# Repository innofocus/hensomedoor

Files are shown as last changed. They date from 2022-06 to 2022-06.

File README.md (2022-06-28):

# hensomedoor
An handsome door for any hen house.
## Object
This is an automated servo mecanism based on internal weight sensor. The prototype served as an chicken house door.

## Principle
The main concept here is the servo's frame as a scale load strain gauge cell based :
hensomedoor v3 1_load_cell

## Description
A load is attached with a string on the axel of the servo to be driven up and down.
The servo is mounted on a load cell with strain-gauge sensor based frame.  
When apparent weight changes, the program reacts consequently.  

The code as the ability to sense the apparente weight of the servo's load (a wood door for instance) and decide what would be done :
- When the weight increases, the load arrives at maximum position, then stop the servo and set maximum position reached.
- When the weight decreases, the load arrives at minimum position, then stop the servo and set minimum position reached.
proto

## Features
The demonstration code is able to do :
- Connect to Wifi
- Web configuration with web interface
- Save the configuration to eeprom
- MQTT: send weight measured at the load cell to an mqtt server with influxdb and grafana for consultation or survey.
- Auto Setup: the current time and date setup at start from a public google script (seen gs/today) - publish at https://script.google.com/macros/s/AKfycby4gVz61EkTZBC5z9TyoYlJeNqo9d11Pdx8pyHc9pY9mqzpYZr4/exec
- Future ability to use google calendar for long scheduling, or sun dawn/rise synchronisation
- OTA update : in order to update the firmware without any cable

## web interface
The main page allows to:
- open or close the door
- read the weight
- read the current status open/close
- set opening and closing time schedule
pageroot

The config page let:
- fine tune parameters
- open or close by increment
- tare the load weight
- play with detector's parameters
config

## Building one
List of materials:
- ESP8266
- SG10 servo motor
- voltage regulators for ESP and servo
- HX711 module
- 4 strain gauge resistors
- cyanoacrylate to glue strain gauge resistors on load cell 3D printed frame.
- tiny wires for strain gauge soldering (ones from wired ear plug are perfect).
See 3D STL files to print the complete box.  

This is my chicken house's door at work :  
opening
closing

## Todos and ongoings
- add electronic schema
- write clean object code

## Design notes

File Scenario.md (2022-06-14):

samplepers = 10
samplenb = 5
sampledur = samplepers / samplenb
stddevmax = 10
speed_slow = 3
speed_fast = 8
w_zero = 10
w_precision = 30
w_delta = 100

# Initialisation
drectioned = 0
tared = 0

## Tare
### setup : door not wooked, no weight
tare = tare
tared = 1

## direction
## setup : door not hooked
## small weight arround 20g (< w_delta) or pinched with fingers
motor_up
while weight not increasing:
directioned = 1

## door weight
motor down 
wait 3
motor stop
w_door = mean(4s)
w_stdd = stdd(4s)

# door weight down
# door time to close
t0
motor down 
while weight == w_door +- w_precision
    mean update
    stdd_update
w_door_down = mean
w_door_down_stdd = stdd
while weight > w_zero
motor stop
t_door_closing = now - t0

# door weight up
# door time to open
t0
motor up
wait 3
while weight == w_door +- w_precision
   mean update
   stdd update
w_door_up = mean
w_door_up_stdd = stdd
while weight < w_door + w_precision + w_delta
    wait
motor stop
t_door_opening = now - t0

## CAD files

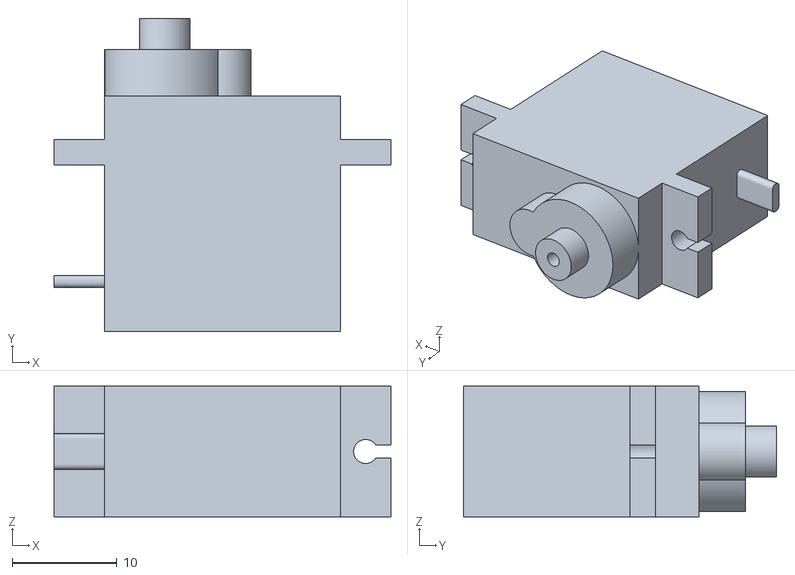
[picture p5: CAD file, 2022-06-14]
stl/hensomedoor v3.1_motor mock.stl
32.3 x 30.0 x 12.5

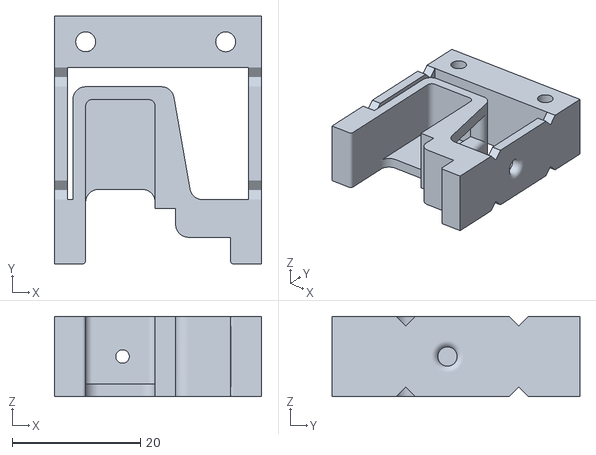
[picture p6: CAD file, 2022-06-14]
stl/hensomedoor v3.1_load_cell.stl
32.3 x 38.6 x 12.5

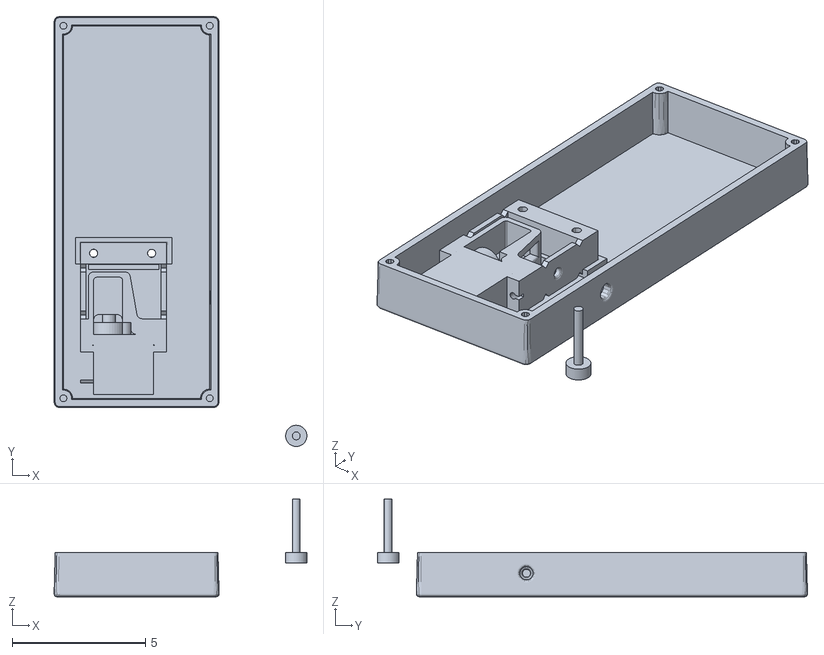
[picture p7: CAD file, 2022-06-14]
stl/hensomedoor v3.1.stl
9.50 x 16.2 x 3.67

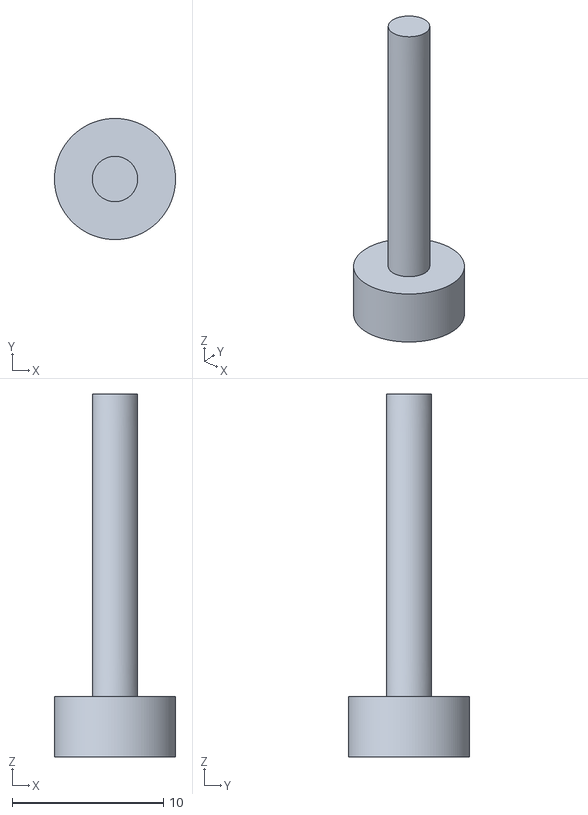
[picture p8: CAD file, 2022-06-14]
stl/hensomedoor v3.1_Part1.stl
8.00 x 8.01 x 24.0

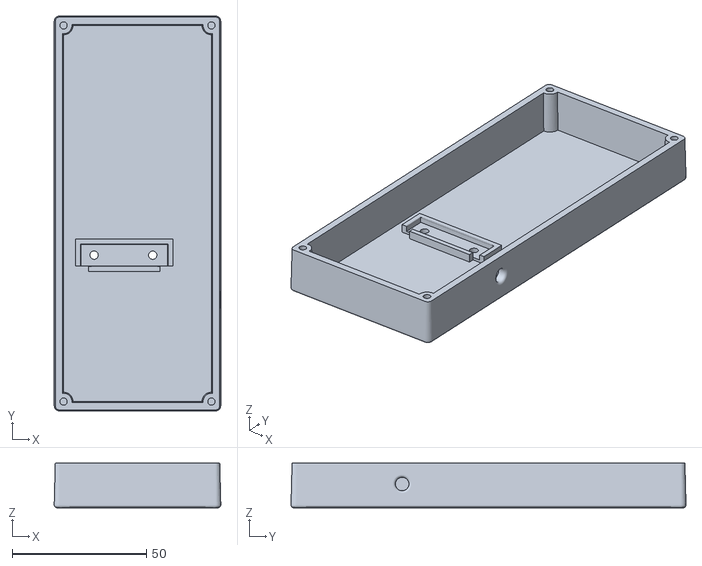
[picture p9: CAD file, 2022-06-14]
stl/hensomedoor v3.1_box_down.stl
62.0 x 147.0 x 16.6

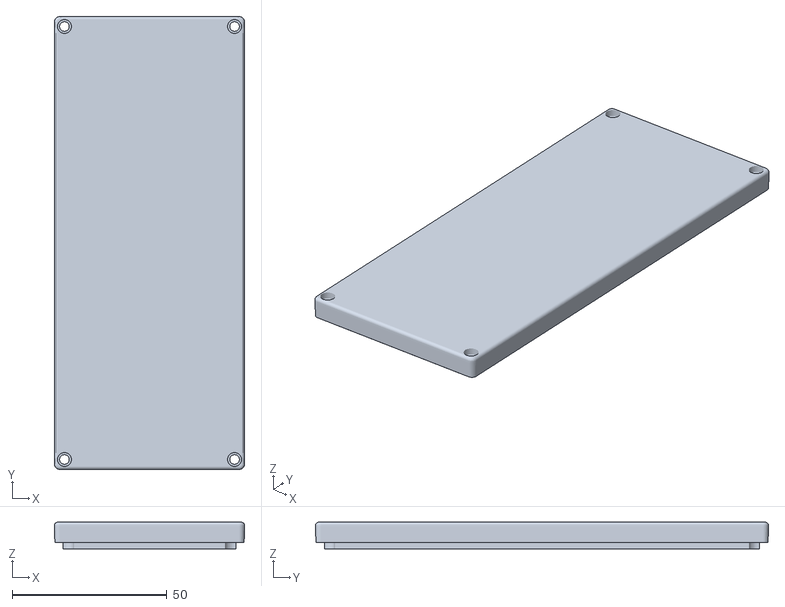
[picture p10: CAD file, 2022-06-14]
stl/hensomedoor v3.1_top_box.stl
61.5 x 146.5 x 8.60

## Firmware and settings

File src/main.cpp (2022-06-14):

#include <Arduino.h>
//networking
#include <ESP8266WiFi.h>
#include <WiFiClient.h>
#include <ESP8266WebServer.h>
#include <ESP8266mDNS.h>
#include <ESP8266HTTPUpdateServer.h>
#include <ArduinoOTA.h>

//ntp
#include <NTPClient.h>
#include <WiFiUdp.h>

//googlescript
#include <HTTPSRedirect/HTTPSRedirect.h>
#include <HTTPSRedirect/DebugMacros.h>

//servo
#include <Servo.h>

//json
#include <ArduinoJson.h>

//timer0 ticker
#include <Ticker.h>

//scale
#include <HX711.h>

//mqtt
#include <PubSubClient.h>

// configuration
#include <EEPROM.h>
#define CONFIG_SIZE 1024
#define CONFCHK 123425321

struct config_st {
  int  confchk;

  char host[32];
  char ssid[32];
  char psk[64];

  char mqttserver[32];
  int  mqttport;
  char mqtttopic[16];

  float scale;
  float scale_offset;
  int  w_closed;
  int  w_precision;
  int  w_delta;
  float  w_stdd_threshold;
  float w_door;
  int w_delta_open;
  int w_delta_close;

  int dooropened;
  int doorclosed;
  int door_h_close;
  int door_m_close;
  int door_h_open;
  int door_m_open;

  int servo_neutral;
  int servo_rotation;
  int speed_slow;
  int speed_fast;

  int configured;
};

config_st config;

// default values
#ifndef HOST

  #define HOST "hensomedoor"
  #define SSID "myssid"
  #define PSK  "myssidpassword"

  #define NTPSERVER "fr.pool.ntp.org"

  #define MQTTSERVER "mymqttserver.somewhere.net"
  #define MQTTPORT 1883
  #define MQTTTOPIC "hensomedoor"

  #define W_ZERO 10
  #define W_PRECISION 10
  #define W_DELTA 100
  #define W_DELTA_OPEN 75
  #define W_DELTA_CLOSE 100
  #define SCALE 3800.0f
  #define SCALE_OFFSET 0.0f
  #define W_DOOR 400
  #define W_STDD_THRESHOLD 1000.0f

  #define DOOR_OPENED false
  #define DOOR_CLOSED false
  #define DOOR_H_CLOSE 19
  #define DOOR_M_CLOSE 00
  #define DOOR_H_OPEN 8
  #define DOOR_M_OPEN 0

  #define SERVO_STOP 92
  #define SERVO_ROTATION -1
  #define SPEED_SLOW 4
  #define SPEED_FAST 10

  #define CONFIGURED 0

  #define SCALE_PERIOD 100
  #define SCALE_MEASURES 10

#endif



//web server
ESP8266WebServer server(80);
ESP8266HTTPUpdateServer httpUpdater;

//ntp
WiFiUDP ntpUDP;

//ntp
NTPClient timeClient(ntpUDP, NTPSERVER, 7200, 60000);

//led
#define LED 4

//motor params
#define SERVO_PIN 2
Servo servo;
Ticker ticker;

//interrupts
#define INTERRUPTPIN 00
volatile byte interrup = false;
int nbinterrupt = 0;

//load cell
// HX711 circuit wiring
#define LOADCELL_DOUT_PIN 13
#define LOADCELL_SCK_PIN 12
#define LOADCELL_SCALE 64
HX711 scale;
float scalevalue;
float scalemean;
float scalestdd;
float scalevalues[SCALE_MEASURES];
int   scaleincreases = false;
int   scaledecreases = false;
int   scaleevolution = 0;
byte scaleindex = 0;


//mqtt
WiFiClient netclient;
PubSubClient mqttclient(netclient);

//RTC
// json from google doc
String json;
int hour_ref;
int min_ref;
int sec_ref;
int hour_now = 0;
int min_now = 0;

//command control
int action_running = false;

//code

void slog(const char msg[]) {
  Serial.println(msg);
}

void save_config() {
  EEPROM.put(0, config);
  if (EEPROM.commit())  {
    slog("save_config done");
  }
  else {
    slog("save_config error");
  }
}


void ConfigPage(const char message[]) {
  digitalWrite(LED, 1);
  const int sizebuf = 2000;
  char temp[sizebuf];
  int sec = millis() / 1000;
  int min = sec / 60;
  int hr = min / 60;

  const char* pageroot = "<html>\
  <head>\
    <meta name=\"viewport\" content=\"width=device-width\" />\
    <title>HSD</title>\
    <style>\
      body { background-color: #cccccc; font-family: Arial, Helvetica, Sans-Serif; Color: #000088; }\
    </style>\
  </head>\
  <body>\
     <h1>Hen Some Door!</h1>\
    <p>Uptime: %02d:%02d:%02d</p>\
    %s\
    <form name=\"config\" method=\"post\" action=\"/config\">\
    <table><tbody>\
      <tr><td>w_stdd_threshold </td><td><input type=\"text\" name=\"w_stdd_threshold\" value=\"%.2f\"></td></tr>\
      <tr><td>servo_neutral </td><td><input type=\"text\" name=\"servo_neutral\" value=\"%d\"></td></tr>\
      <tr><td>w_delta_open </td><td><input type=\"text\" name=\"w_delta_open\" value=\"%d\"></td></tr>\
      <tr><td>w_delta_close </td><td><input type=\"text\" name=\"w_delta_close\" value=\"%d\"></td></tr>\
      <tr><td>w_precision </td><td><input type=\"text\" name=\"w_precision\" value=\"%d\"></td></tr>\
      <tr><td>scale </td><td><input type=\"text\" name=\"scale\" value=\"%.2f\"></td></tr>\
      <tr><td>servo_rotation </td><td><input type=\"text\" name=\"servo_rotation\" value=\"%d\"></td></tr>\
      <tr><td>w_door </td><td><input type=\"text\" name=\"w_door\" value=\"%.0f\"></td></tr>\
      <tr><td>mqttserver </td><td><input type=\"text\" name=\"mqttserver\" value=\"%s\"></td></tr>\
    </tbody></table>\
    <tr><td><input type=\"submit\" value=\"update\">\
    </form>\
    <br>\
    <table><tbody>\
    <tr><td>\
    <form name=\"restore\" method=\"post\" action=\"/restore\"><input type=\"submit\" value=\"restore\"></form>\
    </td><td>\
    <form name=\"tare\" method=\"post\" action=\"/tare\"><input type=\"submit\" value=\"tare\"></form>\
    </td><td>\
    <form name=\"reset\" method=\"post\" action=\"/reset\"><input type=\"submit\" value=\"reset\"></form>\
    </td></tr>\
    <tr><td><form method=\"post\" action=\"/up\"><input type=\"submit\" value=\"UP\"></form>\
    </td><td>\
    <form method=\"post\" action=\"/down\"><input type=\"submit\" value=\"DOWN\"></form>\
    </td></tr>\
    <tr><td>\
    <a href=\"/\">Main Page</a>\
    </td></tr></tbody></table>\
  </body>\
  </html>";
  snprintf(temp, sizebuf, pageroot, hr, min % 60, sec % 60, message, config.w_stdd_threshold,
          config.servo_neutral, config.w_delta_open, config.w_delta_close, config.w_precision,
          config.scale, config.servo_rotation, config.w_door, config.mqttserver);
  server.send(200, "text/html", temp);
  digitalWrite(LED, 0);
}

void handleConfig() {
  if ( server.args() > 0) {
    config.w_stdd_threshold = server.arg("w_stdd_threshold").toInt();
    config.servo_neutral = server.arg("servo_neutral").toInt();
    config.w_closed = server.arg("w_closed").toFloat();
    config.w_door = server.arg("w_door").toFloat();
    config.w_delta = server.arg("w_delta").toInt();
    config.w_delta_open = server.arg("w_delta_open").toInt();
    config.w_delta_close = server.arg("w_delta_close").toInt();
    config.w_precision = server.arg("w_precision").toInt();
    config.scale = server.arg("scale").toFloat();
    config.servo_rotation = server.arg("servo_rotation").toInt();
    config.w_door = server.arg("w_door").toInt();
    strcpy(config.mqttserver, (const char*) server.arg("mqttserver").c_str());
    save_config();
    ConfigPage("Configuration saved");
  }
  else {
    ConfigPage("Welcome to configuration page");
  }
  slog("handleConfig");
}


void setup_config();

void handleRestore () {
  config.confchk = 0;
  save_config();
  setup_config();
  ConfigPage("Configuration defaults restored");
}

void handleReset () {
  server.send(200, "text/html", "reset command commiting");
  delay(2000);
  slog("handleReset");
  ESP.reset();
}

void handleMain(const char message[]) {
  digitalWrite(LED, 1);
  const int sizebuf = 2000;
  char temp[sizebuf];
  int sec = millis() / 1000;
  int min = sec / 60;
  int hr = min / 60;

  char door_status[30];
  if (config.dooropened){
    if (config.doorclosed) {
      strcpy(door_status, "Error");
    }
    else {
      strcpy(door_status, "Opened");
    }
  }
  else {
    if (config.doorclosed) {
      strcpy(door_status, "Closed");
    }
    else {
      strcpy(door_status, "Init");
    }
  }

  const char* pageroot = "<html>\
  <head>\
    <meta http-equiv='refresh' content='5'/>\
    <meta name=\"viewport\" content=\"width=device-width\" />\
    <title>HSD</title>\
    <style>\
      body { background-color: #cccccc; font-family: Arial, Helvetica, Sans-Serif; Color: #000088; }\
    </style>\
  </head>\
  <body>\
    <h1>Hen Some Door!</h1>\
    <p>Time: %02d:%02d</p>\
    <p>Uptime: %02d:%02d:%02d</p>\
    <p>Scale: %d</p>\
    <p>Door: %s</p>\
    %s\
    <tr>\
      <td><form method=\"post\" action=\"/open\"><input type=\"submit\" value=\"Open\"></form></td>\
      <td><form method=\"post\" action=\"/close\"><input type=\"submit\" value=\"Close\"></form></td>\
    </tr>\
    <form name=\"schedule\" method=\"post\" action=\"/schedule\">\
    <table><tbody>\
      <tr><td>Open at </td><td><input type=\"text\" size=\"2\" name=\"door_h_open\" value=\"%02d\">h</td><td><input type=\"text\" size=\"2\" name=\"door_m_open\" value=\"%02d\">m</td></tr>\
      <tr><td>Close at </td><td><input type=\"text\" size=\"2\" name=\"door_h_close\" value=\"%02d\">h</td><td><input type=\"text\" size=\"2\" name=\"door_m_close\" value=\"%02d\">m</td></tr>\
    </tboody></table>\
    <input type=\"submit\" value=\"Schedule!\">\
    </form>\
    <br>\
    <a href=\"/config\">Config</a>\
  </body>\
  </html>";
  snprintf(temp, sizebuf, pageroot, hour_now, min_now, hr, min % 60, sec % 60, (int) scalevalue, door_status, message,
          config.door_h_open, config.door_m_open, config.door_h_close, config.door_m_close);
  server.send(200, "text/html", temp);
  digitalWrite(LED, 0);
}

void handleRoot() {
  handleMain("Welcome");
}

void handleSchedule () {
    if ( server.args() > 0) {
    config.door_h_close = server.arg("door_h_close").toInt();
    config.door_m_close = server.arg("door_m_close").toInt();
    config.door_h_open = server.arg("door_h_open").toInt();
    config.door_m_open = server.arg("door_m_open").toInt();
    save_config();
    handleMain("Schedule saved");
  }
  else {
    handleMain("No data to schedule");
  }
  slog("handleSchedule");
}

// scale functions

float scale_mean() {
  int i;
  float mean = 0;
  for (i=0; i < SCALE_MEASURES; i++) {
    mean = mean + scalevalues[i];
  }
  scalemean = mean / SCALE_MEASURES;;
  return scalemean;
}

float scale_stdd() {
  int i;
  float dev = 0.0f;
  for (i=0; i < SCALE_MEASURES; i++) {
    dev = dev + (scalevalues[i] - scalemean) * (scalevalues[i] - scalemean);
  }
  scalestdd = dev/SCALE_MEASURES;
  return scalestdd;
}

int scale_changes() {
  if (scalestdd > config.w_stdd_threshold) {
    return true;
  }
  else {
    return false;
  }
}

void scale_logger() {
  char str[200];
  snprintf(str, 200, "{ \"scale\": %.0f, \"mean\": %.0f, \"dev\": %.4f, \"action\": %d, \"evol\": %d }", scalevalue, scalemean, scalestdd, action_running, scaleevolution);
  mqttclient.publish(config.mqtttopic,str);
}

float scale_read() {
  if (scale.is_ready()) {
     scalevalue = scale.get_units(1);
  }
  scalevalues[scaleindex] = scalevalue;
  scaleindex++;
  if (scaleindex == SCALE_MEASURES) {
    scaleindex = 0;
  }
  scale_mean();
  scale_stdd();
  scale_logger();
  return scalevalue;
}

int scale_increases() {
  scale_read();
  if (scaleincreases) {
    return true;
  }
  if (scale_changes()) {
    if ( scalevalue > (scalemean + config.w_delta + config.w_precision))  {
      scaleincreases = true;
      return true;
    }
  }
  scaleincreases = false;
  return false;
}

int scale_decreases() {
  scale_read();
  if (scaledecreases) {
    return true;
  }
  if (scale_changes()) {
    if ( scalevalue < (scalemean - config.w_delta - config.w_precision)) {
      scaledecreases = true;
      return true;
    }
  }
  scaledecreases = false;
  return false;
}

int scale_evolution() {
  scale_read();
  if (scaleevolution != 0) {
    return scaleevolution;
  }
  if (scale_changes()) {
    // -1 if weight decreases when closing
    if ( scalevalue < (scalemean - config.w_delta_close - config.w_precision)) {
      scaleevolution = -1;
      return scaleevolution;
    }
    // +1 if weight increases when opening
    if ( scalevalue > (scalemean + config.w_delta_open + config.w_precision))  {
      scaleevolution = 1;
      return scaleevolution;
    }
  }
  return scaleevolution;
}


// door functions

void stopDoor() {
  servo.write(config.servo_neutral);
  delay(100);
  servo.detach();
  interrup = false;
  slog("shutdoor");
}

void closeDoor() {
  action_running = true;
  scaleevolution = 0;
  servo.attach(SERVO_PIN);
  servo.write(config.servo_neutral+config.speed_fast*config.servo_rotation);
  while ((scale_evolution() == 0) && !interrup) {
    delay(SCALE_PERIOD);
  }
  //wrong direction
  if ( scaleevolution == 1 ) {
    config.servo_rotation = - config.servo_rotation;
    delay(1000);
    closeDoor();
  }

  servo.write(config.servo_neutral-config.speed_slow*config.servo_rotation);
  delay(1500);
  stopDoor();
  config.doorclosed = true;
  save_config();
  slog("closeDoor");
  action_running = false;
}

void openDoor() {
  action_running = true;
  scaleevolution = 0;
  servo.attach(SERVO_PIN);
  servo.write(config.servo_neutral-config.speed_slow*config.servo_rotation);
  delay(1500);
  servo.write(config.servo_neutral-config.speed_fast*config.servo_rotation);
  while ((scale_evolution() == 1) && !interrup) {
    delay(SCALE_PERIOD);
  }
  while ((scale_evolution() == 0) && !interrup) {
    delay(SCALE_PERIOD);
  }
  
  //string tension
  servo.write(config.servo_neutral+config.speed_slow*config.servo_rotation);
  delay(500);
  stopDoor();

  config.dooropened = true;
  save_config();
  slog("openDoor");
  action_running = false;
}

void handleClose() {
  if (! config.doorclosed || config.dooropened) {
    closeDoor();
    server.send(200,"text/html","<body>Door Closed<br><a href=\"/\">Main</a>");
  }
  else {
    server.send(200,"text/html","<body>Door was already Closed !<br><a href=\"/\">Main</a>");
  }
  config.dooropened = false;
  save_config();
  slog("handleClose");
}

void handleOpen() {
  if (! config.dooropened || config.doorclosed) {
    openDoor();
    server.send(200,"text/html","<body>Door Opened<br><a href=\"/\">Main</a>");
  }
  else {
    server.send(200,"text/html","<body>Door was already Opened !<br><a href=\"/\">Main</a>");
  }
  config.doorclosed = false;
  save_config();
  slog("handleOpen");
}

void timeClose() {
  if (! config.doorclosed || config.dooropened) {
    closeDoor();
  }
  config.dooropened = false;
  save_config();
  slog("timeClose");
}

void timeOpen() {
  if (! config.dooropened || config.doorclosed) {
    openDoor();
  }
  config.doorclosed = false;
  save_config();
  slog("timeOpen");
}

void handleDown() {
  action_running = true;
  config.dooropened = false;
  int waitloop = 2000;
  servo.attach(SERVO_PIN);
  servo.write(config.servo_neutral+config.speed_fast*config.servo_rotation);
  while ((!scale_decreases()) || (waitloop < 0)) {
    delay(SCALE_PERIOD);
    waitloop -= 2000/50;
  }
  if (scaledecreases) {
    config.doorclosed = true;
    save_config();
  }
  stopDoor();
  server.send(200, "text/plain", "<body>Down done for 2s.<br><a href=\"/\">Main page</a></body>");
  slog("handleDown");
  action_running = false;
}

void handleUp() {
  action_running = true;
  config.doorclosed = false;
  int waitloop = 2000;
  servo.attach(SERVO_PIN);
  servo.write(config.servo_neutral-config.speed_fast*config.servo_rotation);
  while ((!scale_increases()) || (waitloop < 0)) {
    delay(SCALE_PERIOD);
    waitloop -= 2000/50;
  }
  if (scaleincreases) {
    config.dooropened = true;
    save_config();
  }
  stopDoor();
  server.send(200, "text/plain", "<body>Up done for 2s.<br><a href=\"/\">Main page</a></body>");
  slog("handleUp");
  action_running = false;
}

//interruption

void ICACHE_RAM_ATTR handleInterrupt() {
  interrup = true;
  scaledecreases = true;
  scaleincreases = true;
  scaleevolution = 0;
  config.dooropened = false;
  config.doorclosed = false;
  save_config();
  nbinterrupt++;
}

// handles web

void handleAngle() {
  config.servo_neutral = server.arg("angle").toInt();
  if (servo.attached()) {
    servo.write(config.servo_neutral);
    delay(100);
    servo.detach();
  }
  save_config();
  handleMain("Angle servo neutral saved");
  slog("handleAngle");
}

void handleDelta() {
  config.w_delta = server.arg("delta").toInt();
  save_config();
  handleMain("Delta weight save");
  slog("handleDelta");
}

void setup_scale();

void handleTare() {
  scale.tare(10);
  config.scale_offset = scale.get_offset();
  save_config();
  ConfigPage("HSD Tared !");
  slog("handleTare");
}

void handleTime() {
  digitalWrite(LED, 1);
  server.send(200, "text/plain", (char *) timeClient.getFormattedTime().c_str());
  digitalWrite(LED, 0);
}

void handleNotFound() {
  digitalWrite(LED, 1);
  String message = "File Not Found\n\n";
  message += "URI: ";
  message += server.uri();
  message += "\nMethod: ";
  message += (server.method() == HTTP_GET) ? "GET" : "POST";
  message += "\nArguments: ";
  message += server.args();
  message += "\n";
  for (uint8_t i = 0; i < server.args(); i++) {
    message += " " + server.argName(i) + ": " + server.arg(i) + "\n";
  }
  server.send(404, "text/plain", message);
  digitalWrite(LED, 0);
}



void serial_update(void) {
  if (!mqttclient.connected()) {
    mqttclient.connect(config.mqtttopic);
  }
  char str[100];
  snprintf(str, 100,"servo: %03d, int: %02d",servo.read(), nbinterrupt);
  slog(str);
  snprintf(str, 100,"pin: %02d",digitalRead(INTERRUPTPIN));
  slog(str);
  snprintf(str, 100,"{ \"dooropen\": %d, \"doorclosed\": %d, \"rotation\": %d }", config.dooropened, config.doorclosed, config.servo_rotation);
  mqttclient.publish(config.mqtttopic,str);
  slog(str);
  scale_read();
  snprintf(str, 100,"{ \"scale_evolution\": %d, \"scale_changes\": %d }", scale_evolution(), scale_changes());
  mqttclient.publish(config.mqtttopic,str);
  slog(str);
  snprintf(str, 100,"{ \"scale\": %.0f, \"mean\": %.0f, \"dev\": %.8f }", scalevalue, scalemean, scalestdd);
  mqttclient.publish(config.mqtttopic,str);
  slog(str);
}

//time mgmt

const char* google = "script.google.com";
// Replace with your own script id to make server side changes
const char *GScriptId = "AKfycby4gVz61EkTZBC5z9TyoYlJeNqo9d11Pdx8pyHc9pY9mqzpYZr4";

String url = String("/macros/s/") + GScriptId + "/exec";
HTTPSRedirect* client;

void get_google_time() {
  client = new HTTPSRedirect();
  client->setInsecure();
  client->setContentTypeHeader("application/json");
  bool flag = false;
  for (int i=0; i<5; i++){
    int retval = client->connect(google, 443);
    if (retval == 1) {
       flag = true;
       break;
    }
  }
  if ( flag ) { slog("setup_google done"); }
  else { slog("setup_google ,ot connected"); }

  if (client->GET(url, google)) {
    json = client->getResponseBody();
  }
  else {
    json = "";
  }
  slog((char*) json.c_str());
}

void setup_time(void) {
  get_google_time();
  //StaticJsonDocument<500> doc;
  DynamicJsonDocument doc(2048);

  DeserializationError error = deserializeJson(doc, json);

  // Test if parsing succeeds.
  if (error) {
    slog("Json error!");
    server.send(500, "text/plain", (char *)error.c_str());
    return;
  }
  hour_ref = doc["hour"].as<int16_t>();
  min_ref = doc["minute"].as<int16_t>();
  sec_ref = millis() / 1000;
}

void update_time() {
  int sec = ((millis() / 1000) - sec_ref);
  int min = sec / 60 + min_ref + hour_ref*60;
  if ( (min / 60 ) > 24 ) {
    setup_time();
    sec = ((millis() / 1000) - sec_ref);
    min = sec / 60 + min_ref + hour_ref*60;
  }

  hour_now = (min / 60) % 24;
  min_now = min % 60;
}

void setup_wifi(void) {
  WiFi.mode(WIFI_STA);
  WiFi.begin(config.ssid, config.psk);
  slog("");

  // Wait for connection
  while (WiFi.status() != WL_CONNECTED) {
    delay(1000);
  }
  Serial.print("Connected to ");
  slog(config.ssid);
  Serial.print("IP address: ");
  char temp[16];
  snprintf(temp, 16, "%s", WiFi.localIP().toString().c_str());
  slog(temp);

  if (MDNS.begin(config.host)) {
    slog("MDNS responder started");
  }

}

void setup_ota(void) {

  ArduinoOTA.onStart([]() {
    String type;
    if (ArduinoOTA.getCommand() == U_FLASH) {
      type = "sketch";
    } else { // U_SPIFFS
      type = "filesystem";
    }

    // NOTE: if updating SPIFFS this would be the place to unmount SPIFFS using SPIFFS.end()
    slog("OTA Start updating ");
  });
  ArduinoOTA.onEnd([]() {
    slog("\nOTA End");
  });
  ArduinoOTA.onProgress([](unsigned int progress, unsigned int total) {
    Serial.print(".");
  });
  ArduinoOTA.onError([](ota_error_t error) {
    Serial.printf("Error[%u]: ", error);
    if (error == OTA_AUTH_ERROR) {
      slog("Auth Failed");
    } else if (error == OTA_BEGIN_ERROR) {
      slog("Begin Failed");
    } else if (error == OTA_CONNECT_ERROR) {
      slog("Connect Failed");
    } else if (error == OTA_RECEIVE_ERROR) {
      slog("Receive Failed");
    } else if (error == OTA_END_ERROR) {
      slog("End Failed");
    }
  });
  ArduinoOTA.begin();
  slog("setup_ota done");
}

void setup_interrupt() {
  pinMode(INTERRUPTPIN, INPUT);
  attachInterrupt(digitalPinToInterrupt(INTERRUPTPIN), handleInterrupt, FALLING);
  slog("setup_interrupt");
}

void setup_scale() {
    scale.begin(LOADCELL_DOUT_PIN, LOADCELL_SCK_PIN, LOADCELL_SCALE);
    scale.power_down();
    scale.power_up();
  // scale.power_up();
  // scale.set_gain(64);
  // the setup function runs once when you press reset or power the board
  while ( ! scale.is_ready() ) {
    yield();
  }
  scale.set_scale(config.scale);
  scale.set_offset(config.scale_offset);
  int i;
  for (i=0; i < SCALE_MEASURES; i++) {
    scalevalues[i] = 0.0f;
  }
  slog("setup_scale done");
}
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
void loop(void) {
  // no ntp finally
  // timeClient.update();
  if ( ! action_running ) {
    if (WiFi.status() != WL_CONNECTED) {
      WiFi.begin(config.ssid, config.psk);
      delay(1000);
    }
    ArduinoOTA.handle();
    server.handleClient();
    MDNS.update();
    update_time();
    if ( (hour_now == config.door_h_open) and (min_now == config.door_m_open)) {
      timeOpen();
    }
    if ( (hour_now == config.door_h_close) and (min_now == config.door_m_close)) {
      timeClose();
    }
    if (!mqttclient.connected()) {
      mqttclient.connect(config.mqtttopic);
    }
    serial_update();
  }
  delay(1000);
}
